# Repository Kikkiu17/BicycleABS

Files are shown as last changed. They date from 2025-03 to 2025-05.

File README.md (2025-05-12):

# Il progetto
Alla base del progetto c'è il microcontrollore **STM32F103C6T6**. Ho usato poi un servo **MGR996R** collegato alle pastiglie del freno, l'encoder magnetico **AS5600** per la misura della velocità, un sensore hall **3144EUA** per la misura dell'angolo del freno e uno schermo OLED con controllore SH1106. Il firmware è stato tutto scritto da me, compreso il [driver per lo schermo OLED](https://github.com/Kikkiu17/STM32_SH1106), tranne il driver per l'encoder AS5600. Tutti i pezzi sono stati stampati in 3D in PETG, PLA e TPU con una stampante Bambu Lab A1 Mini.

<p float="left">
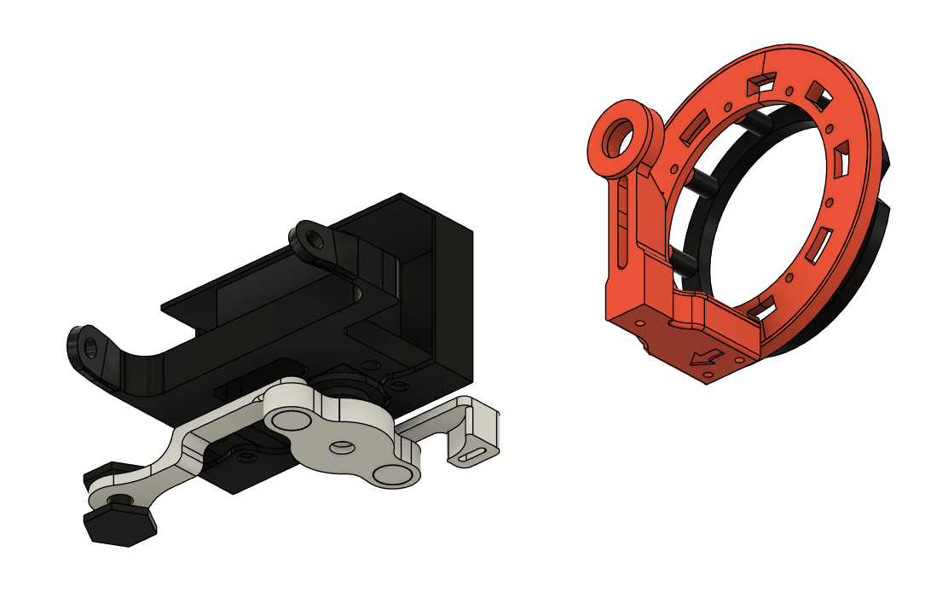
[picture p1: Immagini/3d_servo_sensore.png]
  
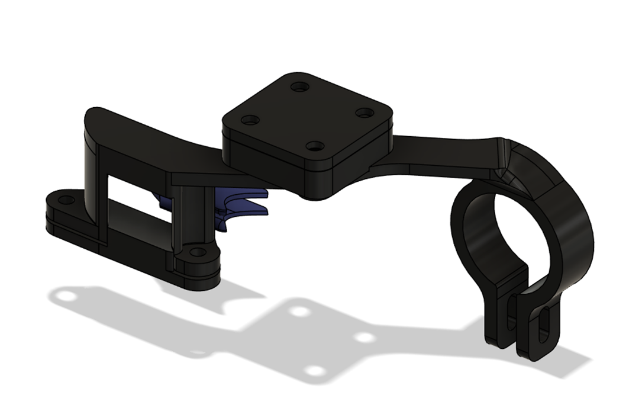
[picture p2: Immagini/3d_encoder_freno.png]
  
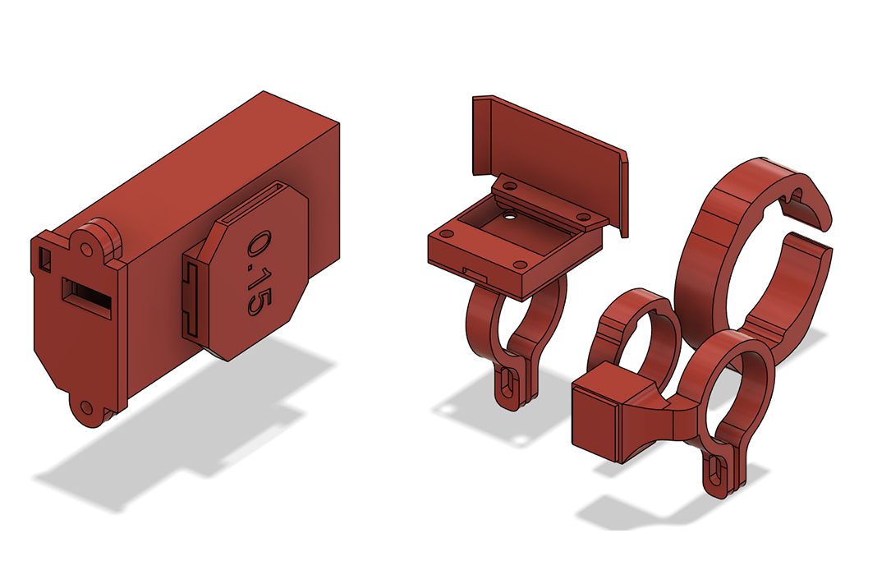
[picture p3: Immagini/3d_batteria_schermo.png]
  
</p>

In base all'angolo della maniglia del freno, il servo applica più o meno pressione alle pastiglie del freno, rallentando quindi la ruota e la bici. Quando la ruota si blocca, ad esempio se si frena tanto sullo sterrato, il microcontrollore rileva questa condizione e rilascia le pastiglie, in modo da sbloccare la ruota. Poi, riapplica pressione in modo da ricominciare a frenare e nel caso il ciclo continua.

Lo schermo OLED posto sul lato destro manubrio permette di vedere la velocità attuale della bici, i chilometri percorsi, il livello della batteria, lo stato delle luci (spente/accese/lampeggianti - la luce frontale, a cui ho tolto la batteria, era compresa con la bici, mentre la luce posteriore è fatta con due LED rossi) e se l'ABS si è attivato. Sul lato sinistro del manubrio invece è posto un pulsante che può essere usato per diverse cose. Se si fa una pressione breve si cambia la modalità delle luci (spente/accese/lampeggianti) in maniera ciclica. Se si fa una pressione lunga si entra nel menù, dal quale si possono modificare varie impostazioni (come l'angolo del servo, che quindi corrisponde alla pressione massima del freno, oppure la luminosità dello schermo), visualizzare diversi parametri di debug (come variabili interne dei TIMER del microcontrollore) e non (come la tensione della batteria).



# Costruzione - Hardware
Lo sviluppo dell'hardware è stato molto impegnativo. Il mio piano era modulare: sarei partito con la cosa più semplice, ovvero il supporto del servo, per fare un sistema **_brake by wire_**. In caso di successo, avrei continuato con il sensore dell'angolo della maniglia del freno (che d'ora in poi chiameremo **sensore freno**). In caso di successo, avrei continuato infine con il sensore di velocità della ruota. In questo modo avrei sprecato meno tempo possibile in caso di fallimento di qualche pezzo.

## Supporto e bracci servo
Per avvitare il supporto alla bici, ho sfruttato due buchi sul telaio apparentemente inutil in una posizione convenientemente vicina alle pastiglie del freno posteriore. Ho creato un supporto molto resistente e molto difficile da piegare in **PETG**, plastica adatta all'uso esterno (resistente ai raggi UV e al calore). Dopo ho realizzato dei bracci corti (in modo da massimizzare la coppia), da avvitare ai bracci del freno esistenti, **_print in place_**, ovvero che non necessitano di assemblaggio dopo la stampa (questo perché sono presenti due cerniere, difficili da fare resistenti e adatte all'assemblaggio). In questo modo il servo rimane ben saldo al telaio della bici e può fare tutta la forza che vuole.

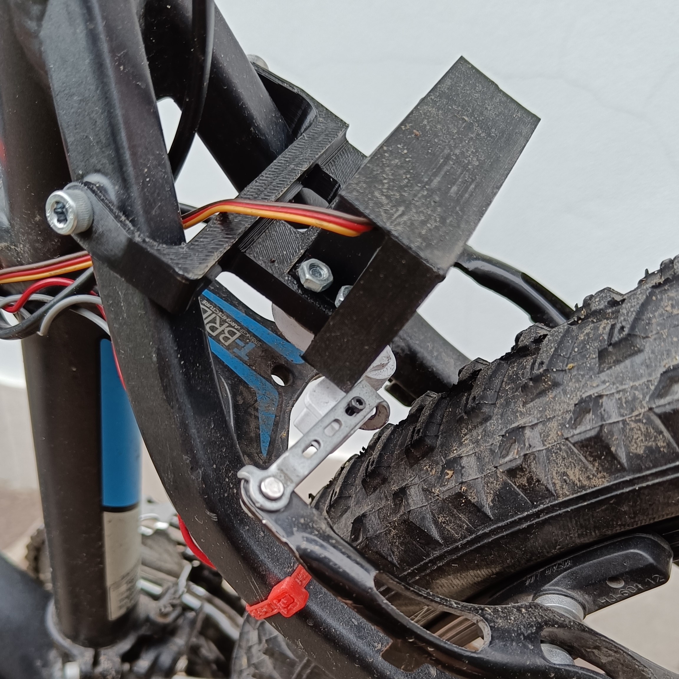
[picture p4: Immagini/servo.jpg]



## Sensore freno
Il sensore consiste in un magnete che ruota e una scheda con un chip che registra l'angolo del campo magnetico prodotto dal sensore. Non c'è però nessun punto comodo in cui montare né la parte fissa (il chip), né quella mobile (il magnete). Per il magnete quindi ho creato una sorta di morsa con dei gommini morbidi (quelli blu nella GIF) avvitata attorno alla maniglia del freno. Questa morsa ha un prolungamento su cui è situato il magnete, che si trova proprio sull'asse di rotazione della maniglia. Per il chip ho creato un supporto da avvitare al manubrio e che si estende fino a sopra il magnete, in modo da poter registrare il suo angolo. In base a quest'angolo, poi, determino l'angolo della maniglia e quindi quanto sto frenando. Dopo alcuni calcoli e controlli quest'angolo viene trasformato nell'angolo servo che viene direttamente inviato a quest'ultimo.



## Sensore di velocità
Il sensore di velocità comprende un semplice sensore **_hall_** (che rileva la presenza di un magnete o meno) e 30 magneti montati su un disco, a sua volta montato sulla ruota posteriore. Misurando quanti magneti vengono rilevati al secondo, si può determinare la velocità della ruota. Anche qui il problema è che non c'è nessun punto di montaggio comodo. Ho dovuto quindi creare il disco arancione in due pezzi in modo da poterlo mettere sull'asse di rotazione senza dover smontare l'intera ruota (il che significherebbe smontare anche il cambio... cosa che non avevo voglia di fare decine di volte) e per tenerlo fisso ad essa ho creato il pezzo nero che va ad avvitarsi dietro. In questo modo il pezzo arancione e il pezzo nero, avvitandosi, vanno a stringersi sui raggi del cerchio della ruota, effettivamente bloccandoli ad essa.

Il supporto del sensore **_hall_** è messo sull'asse della ruota e tenuto fermo con il dado originale che tiene fissa la ruota al telaio.

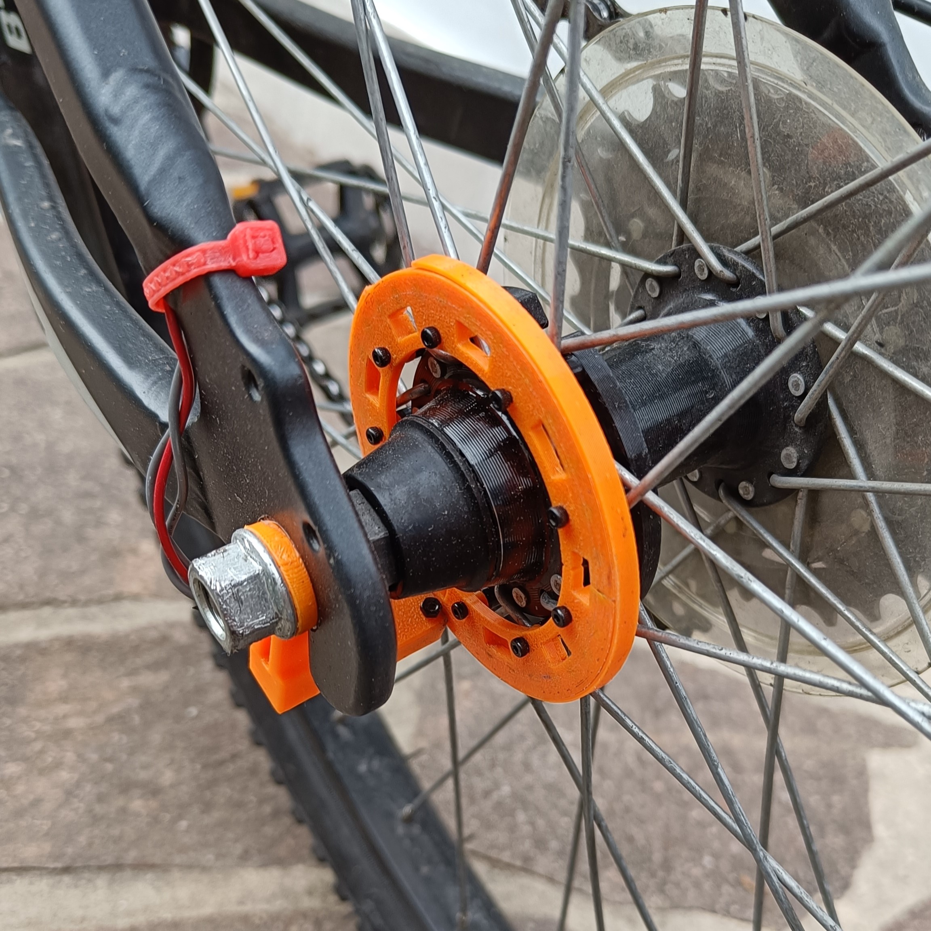
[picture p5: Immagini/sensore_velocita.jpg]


## Batteria
Ho anche creato un contenitore per una batteria LiPo 2S (7.4 V) che contiene anche un modulo per la ricarica della stessa. Ho voluto creare questo contenitore in modo da poter estrarre la batteria dalla bici in modo facile e veloce, così che posso portarla comodamente con me quando devo ricaricarla.



# Circuito elettronico
## Primo prototipo
Ho costruito il primo prototipo di circuito su una scheda millefori contemporaneamente allo sviluppo dei pezzi stampati in 3D. Dopo aver installato tutte le componenti e aver scritto parte del codice, ho realizzato che una scheda del genere non era adatta. Questo perché facendo pressione con il coperchio della scatola della scheda, oppure con qualche vibrazione (ad esempio passando dalla strada al marciapiede), il programma si bloccava e il servo rimaneva nella posizione di massima pressione. Dopo aver cercato per diverso tempo la causa del problema e non avendola trovata, ho deciso di abbandonare lo sviluppo su questa scheda. Questa però non è stata inutile perché mi ha permesso di testare le componenti e il programma, quindi sono passato allo sviluppo di una PCB (era solo un **_proof of concept_**).

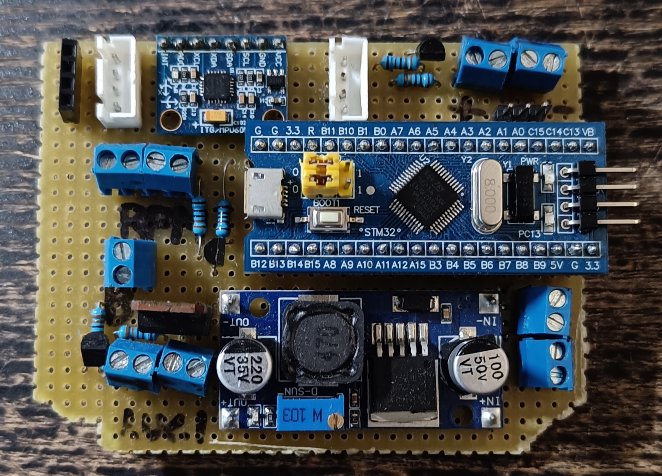
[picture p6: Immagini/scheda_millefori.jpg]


## PCB
Ho creato quindi la PCB con tutti i vari MOSFET per poter controllare la luce frontale e posteriore (luce posteriore che si accende quando si frena, mentre rimane spenta quando non si frena), il servo e il sensore di velocità. Ho messo poi due connettori per collegare lo schermo OLED e il sensore freno via I²C al microcontrollore. Ho lasciato anche dello spazio per il convertitore DC-DC dalla tensione della batteria a 6 V, ovvero la tensione per il servo, aggiungendo poi un altro regolatore di tensione per trasformare questi 6 V in 3.3 V per il microcontrollore.

Ho fatto qualche errore, ovvero che le impronte dei MOSFET non erano corrette, quindi quando ho assemblato la PCB ho dovuto ruotare questi componenti di 90°... però funziona.

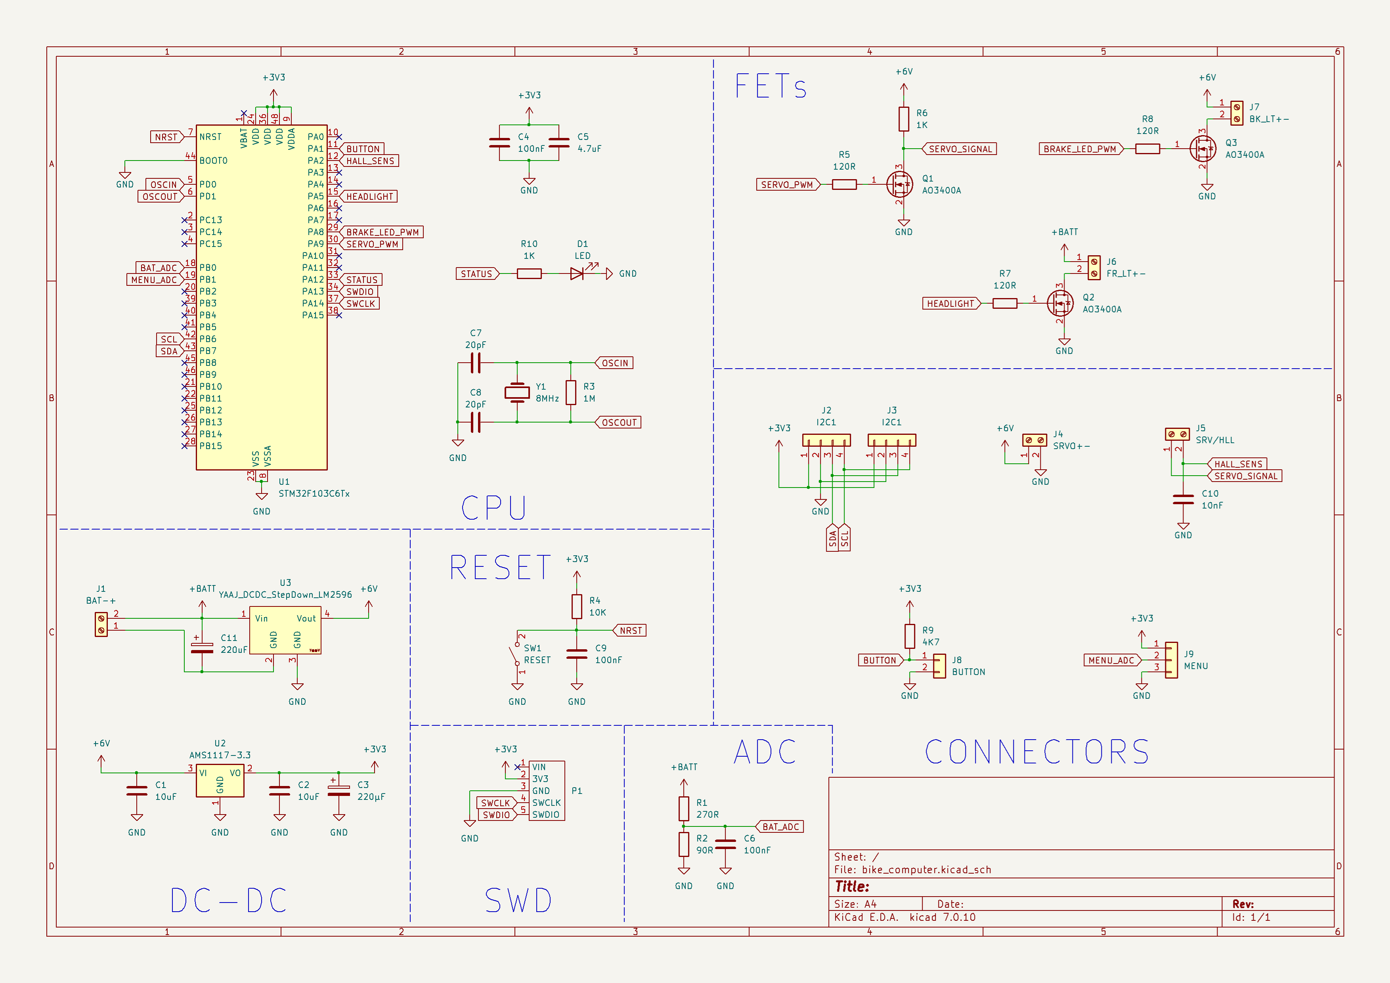
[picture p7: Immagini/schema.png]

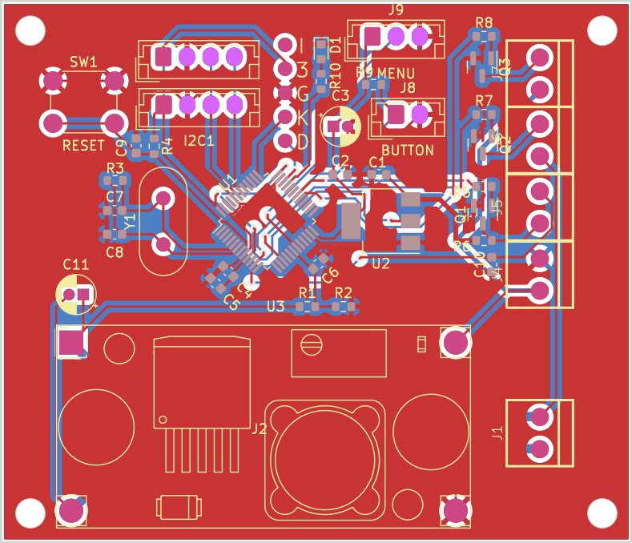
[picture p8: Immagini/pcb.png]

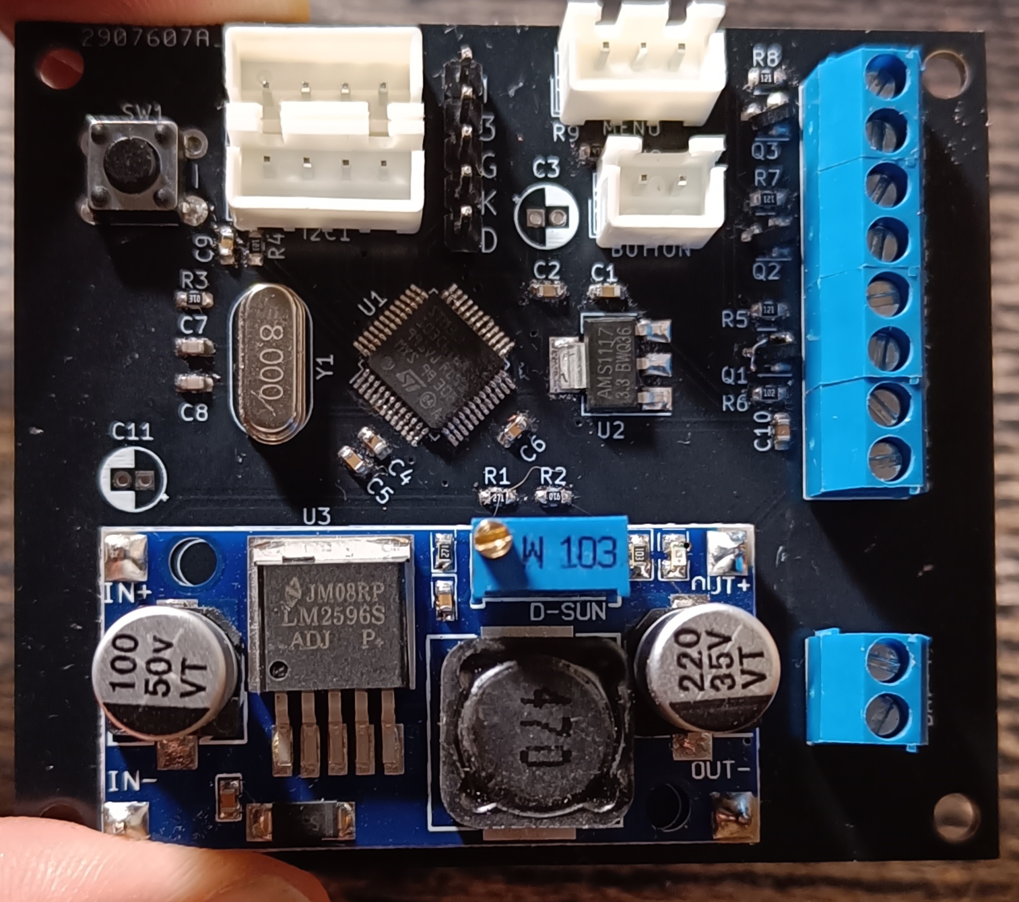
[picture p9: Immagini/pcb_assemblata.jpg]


# Firmware
## Calcolo velocità
L'output del sensore hall sulla ruota è un'onda quadra con un certo periodo. Questo periodo idealmente dovrebbe essere in microsecondi, così la conversione in secondi sarebbe molto semplice. C'è una limitazione: i timer dell'STM32F103 sono a 16-bit, quindi il valore massimo è 65535 - se questi fossero microsecondi, il periodo massimo registrabile sarebbe di circa 65 millisecondi. Facendo $f_{mag}=\frac{1}{T_{hall}}=\frac{1}{0.065}=15.38\text{ Hz}$ otteniamo la frequenza di rilevamento dei magneti dal sensore. Dato che abbiamo 30 magneti: $f_{ruota}=\frac{f_{mag}}{30}=\frac{15.38}{30}=0.51\text{ Hz}$.

Questo è un moto circolare, quindi per calcolare la velocità tangenziale bisogna fare: $v_{ruota}=\frac{r\Delta\theta}{\Delta t}=r\Delta\theta f_{ruota}$. Visto che abbiamo il periodo di un'intera rotazione, consideriamo che l'arco sia la circonferenza della ruota: $\Delta\theta=\frac{arco}{raggio}=\frac{2\pi r}{r}=2\pi$, quindi la formula iniziale diventa: $v_{ruota}=2\pi rf_{ruota}$.

Ora possiamo finalmente vedere la velocità minima registrabile, col periodo massimo di 65 millisecondi, ovvero 0.51 Hz. Considerando il raggio della ruota $r=0.34\text{ m}$: $v_{ruota}=2\pi (0.34\text{ m})(0.51\text{ Hz})=1.08\text{ m/s}$ ovvero 3.9 km/h. Questa è una velocità minima un po' troppo alta e quindi sarebbe difficile rilevare quando la ruota è effettivamente ferma.

Dobbiamo quindi aumentare il periodo massimo registrabile. Fino ad ora, abbiamo considerato che un "tick" equivalga a un microsecondo, ma ora dobbiamo farlo valere di più: ad esempio, se 1 tick = 2 microsecondi, allora il periodo massimo registrabile sarebbe il doppio, ovvero 130 millisecondi e utilizzando la formula di prima la velocità minima sarebbe di 1.97 km/h che è già più accettabile. Per fare questo calcolo nel software, dobbiamo considerare la frequenza del clock del timer, che è uguale per tutte le periferiche `APB1` e in questo caso è di `64 MHz`. Il valore di ogni tick è dato dalla frequenza di clock del timer diviso il "prescaler" `PSC`. Quindi, se il prescaler fosse di 128, avremmo $f_{TIM}=\frac{64000000}{128}=500\text{ kHz}$ quindi il tick sarebbe di 2 microsecondi. Ora dividiamo la frequenza di ogni tick per il numero di tick registrati ($k_{hall}$) e otteniamo la frequenza dei magneti.

Quindi:

$f_{TIM}=\frac{f_{APB1}}{PSC}$

$f_{mag}=\frac{f_{TIM}}{k_{hall}}$

$f_{ruota}=\frac{f_{mag}}{30}=\frac{\frac{f_{TIM}}{k_{hall}}}{30}=\frac{\frac{\frac{f_{APB1}}{PSC}}{k_{hall}}}{30}$ -> questa è infine, facendo qualche semplificazione, la formula usata nel programma, in C: `freq = ((float)(apb1_timer_clock / 10 / ((TIM2->PSC + 1) / 1000)) / (float)period) / 30.0` da cui si ricava la velocità.
## Rilevamento blocco
Ci sono due timer in azione: il primo è quello che è stato usato finora per calcolare la velocità della ruota. Il secondo viene usato per il rilevamento del blocco di essa. Il secondo timer ha una frequenza di 20 Hz, quindi viene controllato se la ruota è bloccata ogni 50 ms. Ogni 50 ms, quindi, il secondo timer controlla il periodo del primo timer: se questo è troppo alto, ovvero più alto del periodo del secondo timer, significa che la ruota ha rallentato molto, quindi si può considerare che stia scivolando. Inoltre, il primo timer, ogni volta che il sensore hall rileva un magnete, resetta il valore del secondo timer, quindi il rilevamento del blocco è migliore. L'ABS, quindi, se la ruota scivola, si attiva.

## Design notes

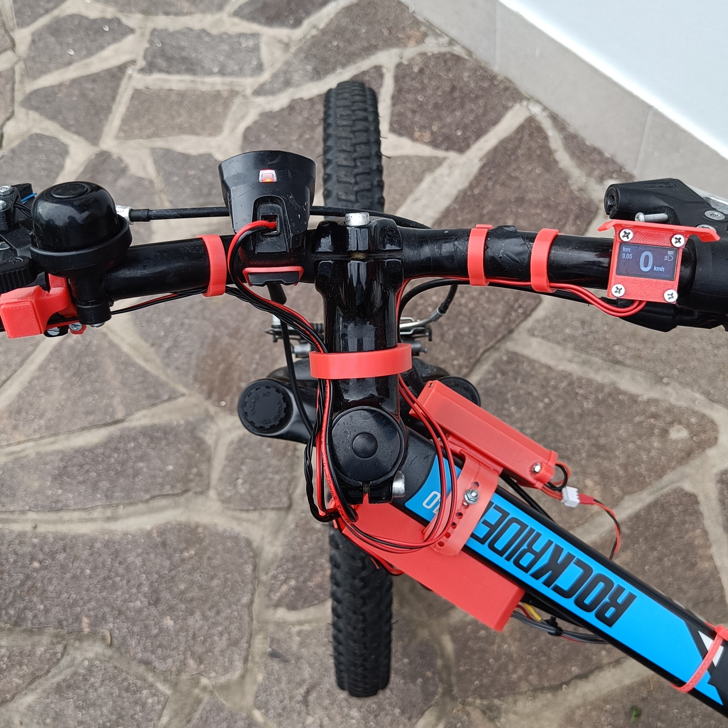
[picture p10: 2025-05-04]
Immagini/manubrio.jpg

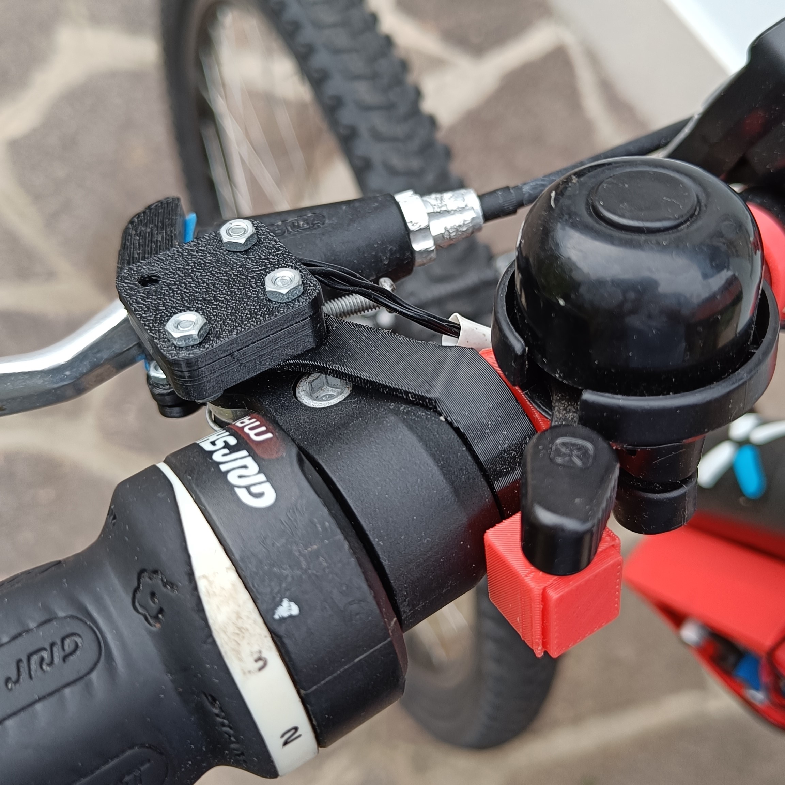
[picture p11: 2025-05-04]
Immagini/encoder_freno.jpg

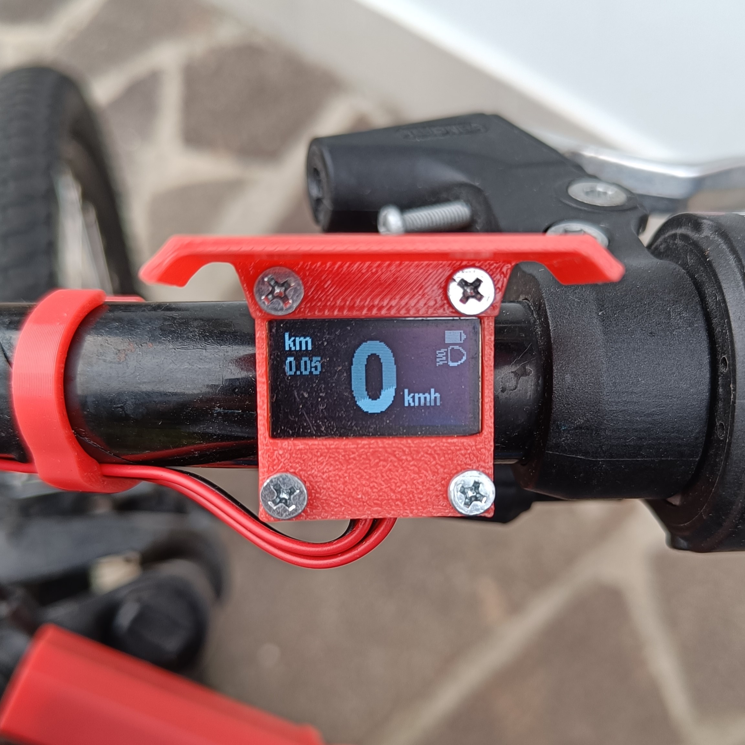
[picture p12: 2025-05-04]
Immagini/schermo.jpg

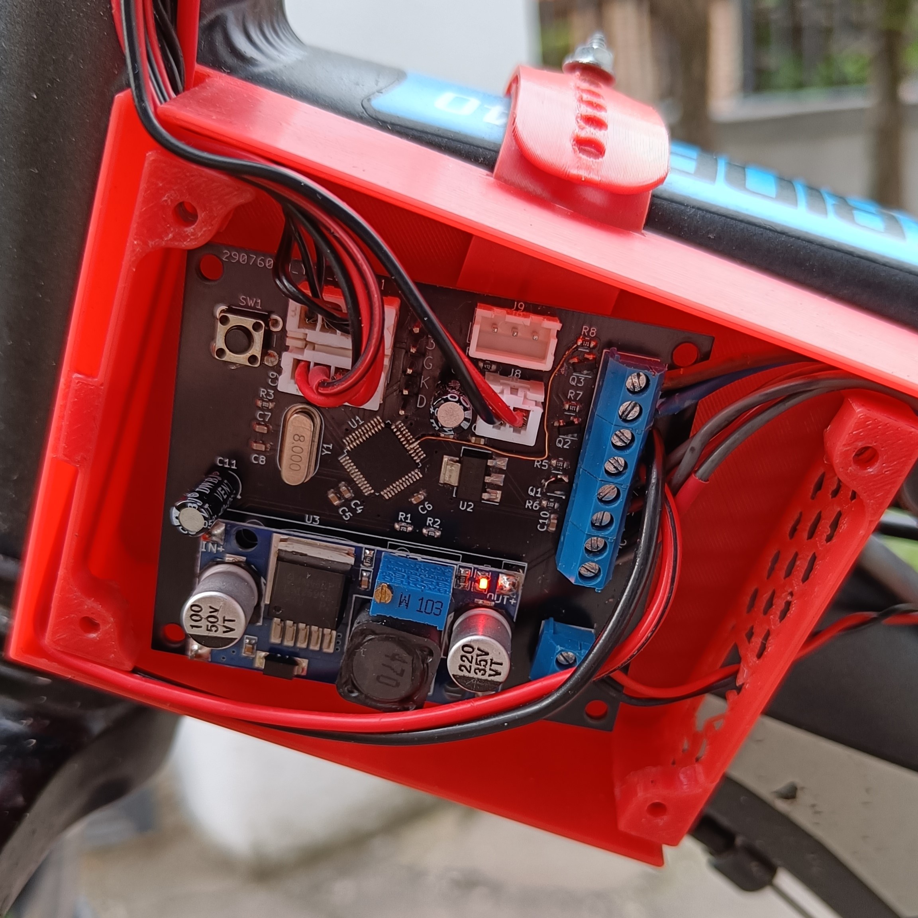
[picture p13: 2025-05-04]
Immagini/pcb_montata.jpg

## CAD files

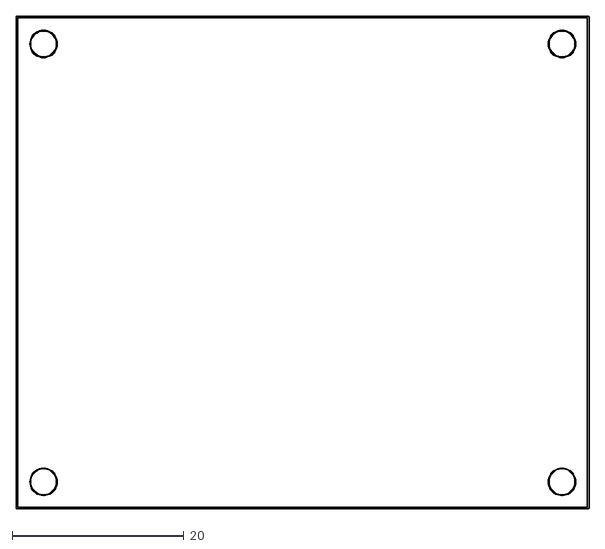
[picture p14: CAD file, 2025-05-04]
Hardware/PCB/bike_computer_gerber/bike_computer-Edge_Cuts.dxf
66.8 x 57.5

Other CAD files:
Hardware/PCB/bike_computer_gerber/bike_computer-F_Paste.dxf

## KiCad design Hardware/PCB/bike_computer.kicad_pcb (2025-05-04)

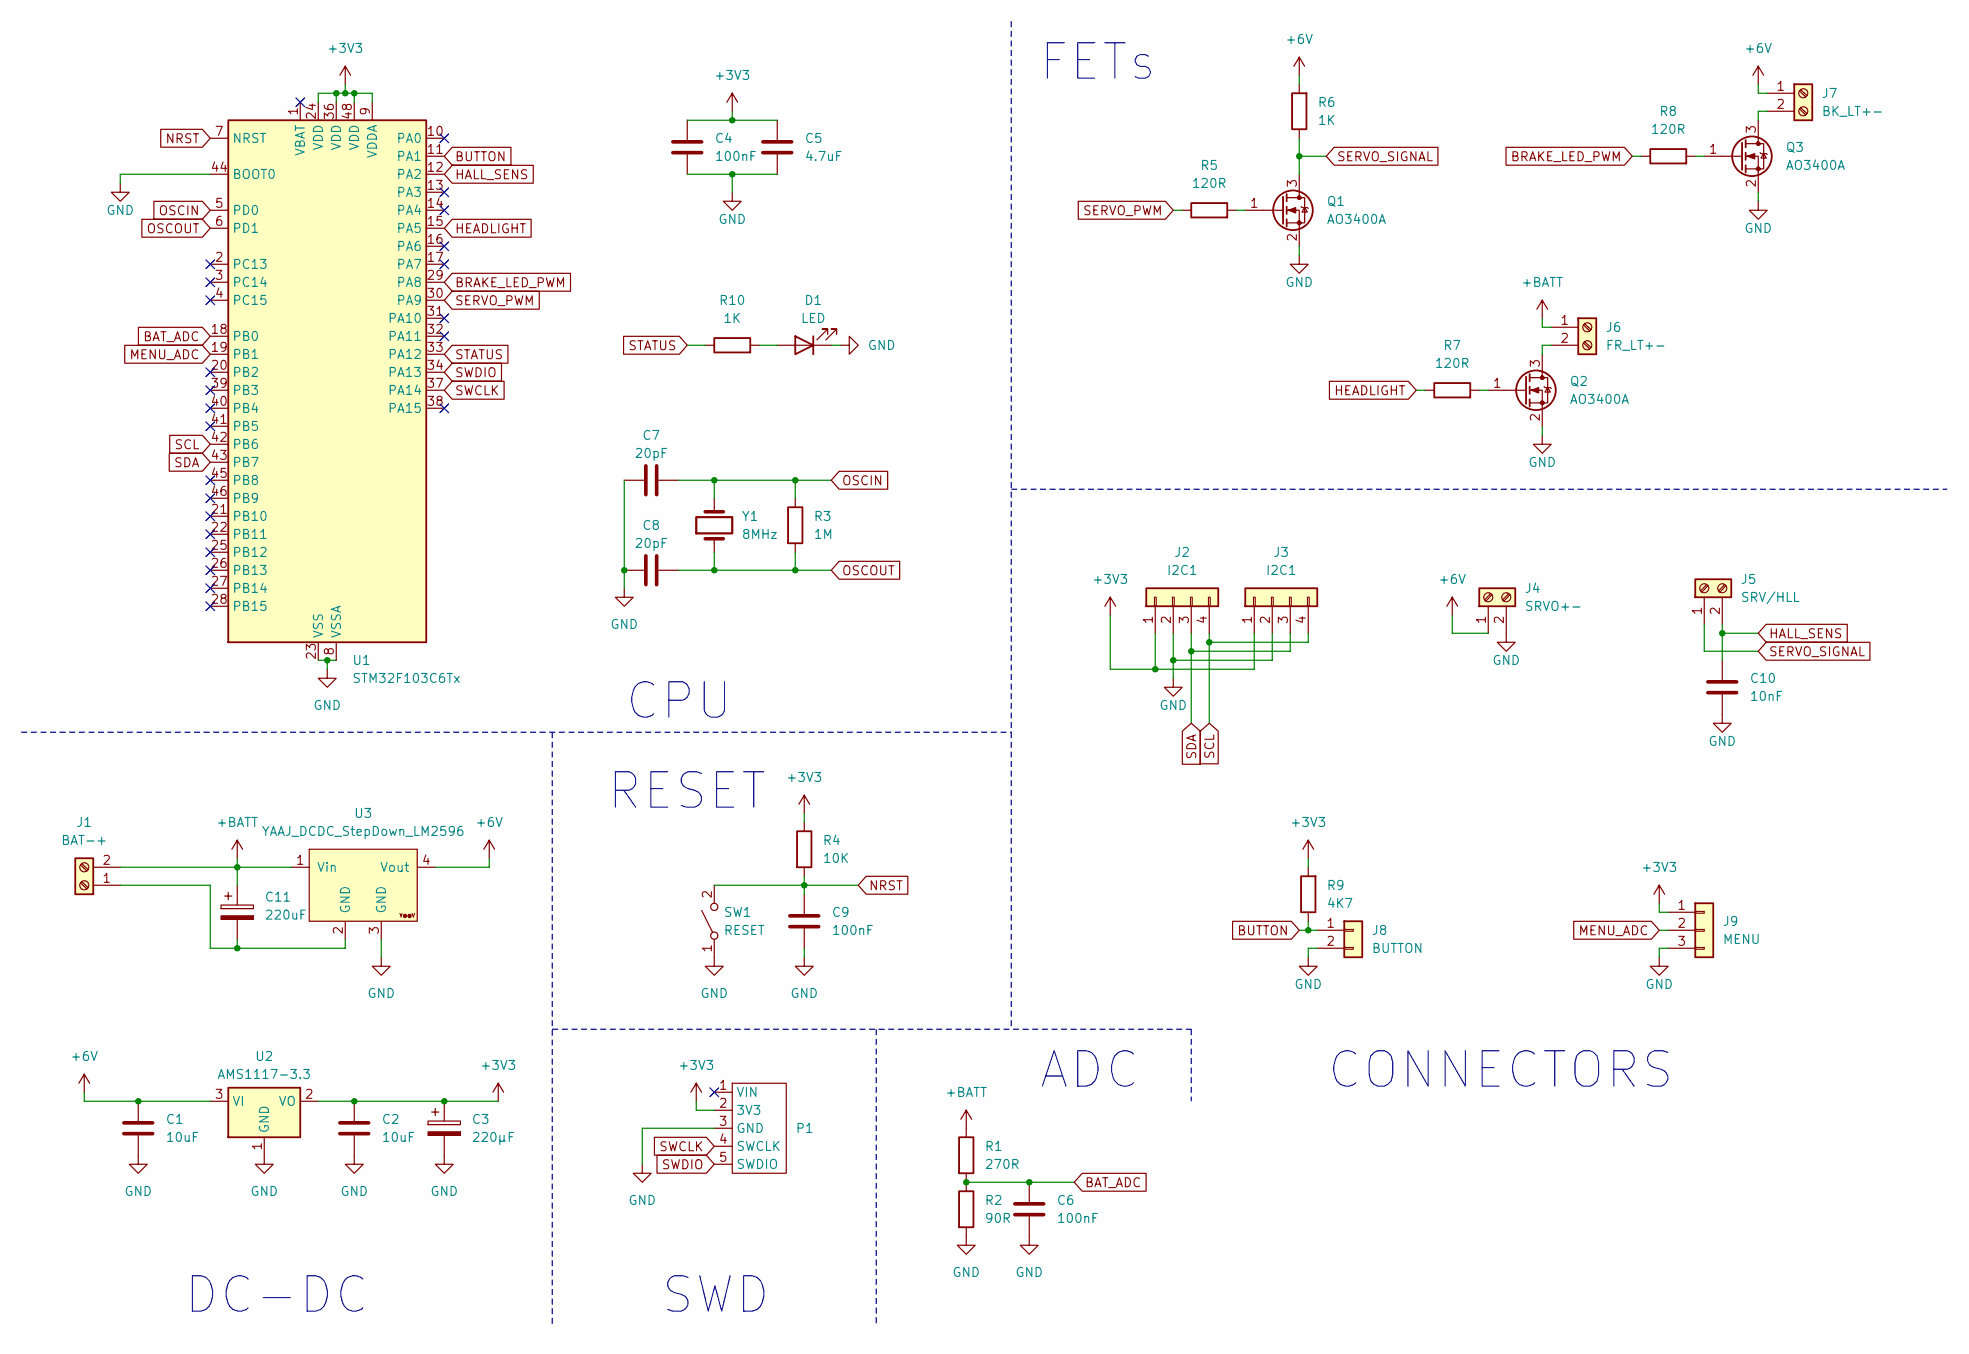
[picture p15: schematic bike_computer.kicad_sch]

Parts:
C1, C2: 10uF; C_0603_1608Metric
C3: 220µF; CP_Radial_D4.0mm_P1.50mm
C4, C6, C9: 100nF; C_0603_1608Metric
C5: 4.7uF; C_0603_1608Metric
C7, C8: 20pF; C_0603_1608Metric
C10: 10nF; C_0603_1608Metric
C11: 220uF; CP_Radial_D4.0mm_P1.50mm
D1: LED; LED_0603_1608Metric
J1: BAT-+; screw_2p_small
J2, J3: I2C1; JST_EH_B4B-EH-A_1x04_P2.50mm_Vertical
J4: SRVO+-; screw_2p_small
J5: SRV/HLL; screw_2p_small
J6: FR_LT+-; screw_2p_small
J7: BK_LT+-; screw_2p_small
J8: BUTTON; JST_EH_B2B-EH-A_1x02_P2.50mm_Vertical
J9: MENU; JST_EH_B3B-EH-A_1x03_P2.50mm_Vertical
P1: stm_headers
Q1, Q2, Q3: AO3400A; SOT-23
R1: 270R; R_0603_1608Metric
R2: 90R; R_0603_1608Metric
R3: 1M; R_0603_1608Metric
R4: 10K; R_0603_1608Metric
R5, R7, R8: 120R; R_0603_1608Metric
R6, R10: 1K; R_0603_1608Metric
R9: 4K7; R_0603_1608Metric
SW1: RESET; SW_PUSH_6mm
U1: STM32F103C6Tx; LQFP-48_7x7mm_P0.5mm
U2: AMS1117-3.3; SOT-223-3_TabPin2
U3: YAAJ_DCDC_StepDown_LM2596
Y1: 8MHz; Crystal_HC49-4H_Vertical

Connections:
+3V3: C2.1, C3.1, C4.1, C5.1, J2.1, J3.1, J9.1, P1.2 (3V3), R4.1, R9.2, U1.9 (VDDA), U1.24 (VDD), U1.36 (VDD), U1.48 (VDD), U2.2 (VO)
+6V: C1.1, J4.1, J7.1, R6.2, U2.3 (VI), U3.4 (Vout)
+BATT: C11.1, J1.2, J6.1, R1.1, U3.1 (Vin)
BAT_ADC: C6.1, R1.2, R2.1, U1.18 (PB0)
BRAKE_LED_PWM: R8.1, U1.29 (PA8)
BUTTON: J8.1, R9.1, U1.11 (PA1)
GND: C1.2, C2.2, C3.2, C4.2, C5.2, C6.2, C7.1, C8.1, C9.2, C10.2, D1.1 (K), J2.2, J3.2, J4.2, J8.2, J9.3, P1.3 (GND), Q1.2 (S), Q2.2 (S), Q3.2 (S), R2.2, SW1.1 (A), U1.8 (VSSA), U1.23 (VSS), U1.35 (VSS), U1.44 (BOOT0), U1.47 (VSS), U2.1 (GND), U3.3 (GND)
HALL_SENS: C10.1, J5.2, U1.12 (PA2)
HEADLIGHT: R7.1, U1.15 (PA5)
MENU_ADC: J9.2, U1.19 (PB1)
NRST: C9.1, R4.2, SW1.2 (B), U1.7 (NRST)
unnamed: C11.2, J1.1, U3.2 (GND)
unnamed: D1.2 (A), R10.2
unnamed: Q1.1 (G), R5.2
unnamed: J6.2, Q2.3 (D)
unnamed: Q2.1 (G), R7.2
unnamed: J7.2, Q3.3 (D)
unnamed: Q3.1 (G), R8.2
OSCIN: C7.2, R3.1, U1.5 (PD0), Y1.2
OSCOUT: C8.2, R3.2, U1.6 (PD1), Y1.1
SCL: J2.4, J3.4, U1.42 (PB6)
SDA: J2.3, J3.3, U1.43 (PB7)
SERVO_PWM: R5.1, U1.30 (PA9)
SERVO_SIGNAL: J5.1, Q1.3 (D), R6.1
STATUS: R10.1, U1.33 (PA12)
SWCLK: P1.4 (SWCLK), U1.37 (PA14)
SWDIO: P1.5 (SWDIO), U1.34 (PA13)

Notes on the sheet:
FETs
CPU
RESET
ADC
DC-DC
SWD
CONNECTORS

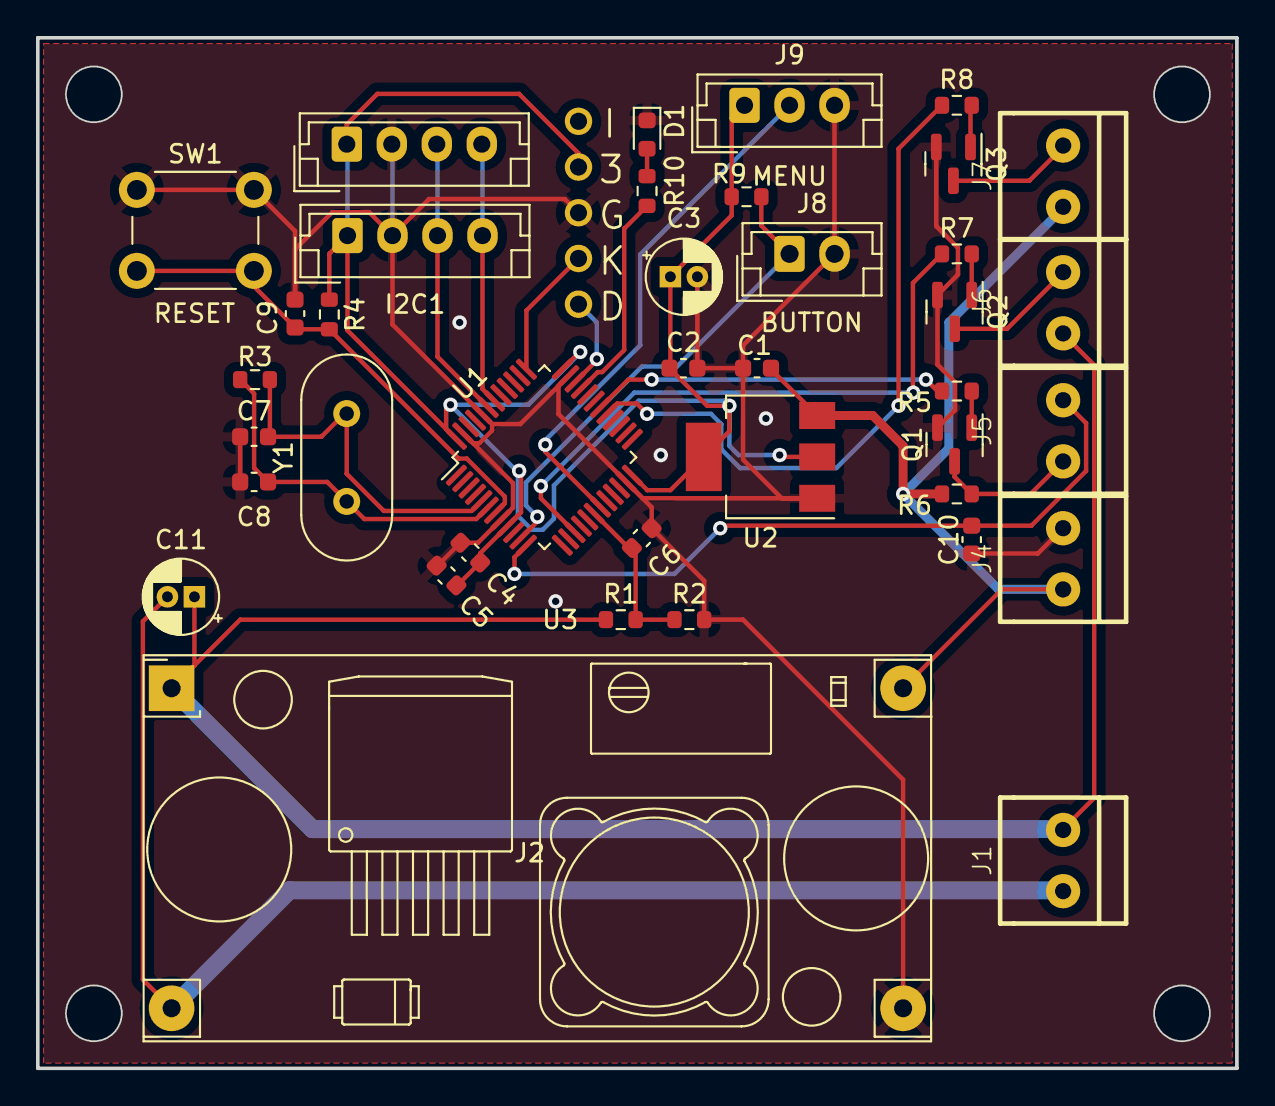
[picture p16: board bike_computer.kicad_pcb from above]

Board: 2 copper layers, 66.6 x 57.3 mm, 40 parts (0 on the bottom side), 27 nets.

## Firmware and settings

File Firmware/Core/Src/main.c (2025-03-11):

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
/* Includes ------------------------------------------------------------------*/
#include "main.h"
#include "adc.h"
#include "i2c.h"
#include "tim.h"
#include "gpio.h"

/* USER CODE BEGIN Includes */
#include <inttypes.h>
#include <stdio.h>
#include <stdlib.h>
#include "As5600.h"
#include "servo.h"
#include "stm32f1xx_ll_exti.h"

#include "../sh1106/sh1106.h"
#include "../bitmaps/bitmaps.h"
#include "../menu/menu.h"
#include "../settings.h"
#include "../button/button.h"
/* USER CODE END Includes */


/* USER CODE BEGIN PV */
uint32_t kmh = 0;
int32_t last_kmh = 0;
int32_t kmh_diff = 0;
uint32_t brake_lever_angle = 0;
int32_t servo_angle = 0;
int32_t min_servo_angle = 0;

bool abs_on = false;				// if true, the ABS is currently operating
uint32_t abs_time = 0;			// time of the ABS activation

uint64_t apb1_timer_clock = 0;
uint64_t timer_update_constant = 0;
uint64_t period = 0;
uint32_t last_period = 0;
uint32_t last_capture_time = 0;

uint32_t light_mode = 0;

uint32_t last_capture_value = 0;
float last_freq = 0.00;
float current_freq = 0.00;
float avg_freq = 0.00;

char text[50];
/* USER CODE END PV */

void SystemClock_Config(void);
/* USER CODE BEGIN 0 */
long mapInt(uint32_t x, int32_t in_min, int32_t in_max, int32_t out_min, int32_t out_max) {
  return (x - in_min) * (out_max - out_min) / (in_max - in_min) + out_min;
}


uint32_t constrain(uint32_t value, uint32_t max, uint32_t min)
{
	if (value >= max)
		return max;
	else if (value <= min)
		return min;
	return value;
}


uint32_t offset(uint32_t value, uint32_t offset)
{
	if (value <= offset)
		return 0;
	else
		return value - offset;
}

/* USER CODE END 0 */

/**
  * @brief  The application entry point.
  * @retval int
  */
int main(void)
{

  /* MCU Configuration--------------------------------------------------------*/

  /* Reset of all peripherals, Initializes the Flash interface and the Systick. */
  HAL_Init();

  /* Configure the system clock */
  SystemClock_Config();

  /* Initialize all configured peripherals */
  MX_GPIO_Init();
  MX_TIM1_Init();
  MX_TIM2_Init();
  MX_TIM3_Init();
  MX_I2C1_Init();
  MX_ADC1_Init();
  /* USER CODE BEGIN 2 */
  HAL_TIM_PWM_Start(&htim1, TIM_CHANNEL_1);
  HAL_TIM_PWM_Start(&htim1, TIM_CHANNEL_2);
  HAL_TIM_IC_Start_IT(&htim2, TIM_CHANNEL_3);
  //HAL_TIM_PWM_Start(&htim3, TIM_CHANNEL_1);
  HAL_TIM_Base_Start_IT(&htim3);
  HAL_ADCEx_Calibration_Start(&hadc1);

  apb1_timer_clock = HAL_RCC_GetPCLK1Freq() * 2 / 100;
  timer_update_constant = (TIM3->PSC + 1) * (TIM3->ARR + 1) * (720 / ((TIM2->PSC + 1) / 1000));

  SERVO_Write(&htim1, TIM_CHANNEL_2, servo_max, 1);

  SH1106_Init();
  SH1106_SetBrightness(screen_brightness);
  SH1106_ClearScreen();

  AS5600_TypeDef as5600;
  AS5600_Init();
  Get_Magnet_Status(&as5600);
  bool magnet_status = as5600.Status_Magnet;

  if (magnet_status) SH1106_WriteChars(0, 0, "magnete ok", 10, Arial_12pt, 1);
  else
  {
	  SH1106_WriteChars(0, 0, "Magnete NON OK\nPremi un tasto\nper continuare", 44, Arial_12pt, 1);
	  while (1)
	  {
		  if (!HAL_GPIO_ReadPin(BTN_IN_GPIO_Port, BTN_IN_Pin))
			  break;
	  }
  }

  SH1106_ClearScreen();
  SH1106_SetScreenAutoUpdate(false);

  uint32_t flashing_lights_time = 0;
  uint32_t deltat = 0;
  uint32_t last_time = 0;
  float traveled_meters = 0.00;
  uint32_t mvbat = 0;
  bool show_low_bat = false;
  char decimal_travel_string[2];
  uint32_t raw_brake_lever_angle = 0;
  /* USER CODE END 2 */

  /* Infinite loop */
  /* USER CODE BEGIN WHILE */
  while (1)
  {
	  deltat = uwTick - last_time;
	  last_time = uwTick;

	  // clear screen
	  SH1106_FillScreen(BLACK);

	  Get_Raw_Angle(&as5600);
	  raw_brake_lever_angle = as5600.Raw_sensor_Angle;
	  brake_lever_angle = offset(raw_brake_lever_angle, BRAKE_ANGLE_OFFSET);

	  if (!abs_on)
	  {
		  servo_angle = mapInt((int16_t)(brake_lever_angle), 0, BRAKE_ANGLE_MAX, servo_max, servo_min);
		  servo_angle = constrain(servo_angle, servo_max, servo_min);
	  }
	  else
	  {
		  // increase brake pressure gradually
		  if (servo_angle - SERVO_ABS_BRAKE_RATE > min_servo_angle && min_servo_angle >= servo_min)
			  servo_angle -= SERVO_ABS_BRAKE_RATE;
		  else abs_on = false;
	  }

	  if (mvbat > LOW_BATTERY_THRESHOLD)
	  {
		  if (servo_enabled)
			  SERVO_Write(&htim1, TIM_CHANNEL_2, servo_angle, 1);
		  else
		  {
			  if (!servo_hold)
				  SERVO_Write(&htim1, TIM_CHANNEL_2, servo_max, 1);
		  }
	  }
	  else
		  SERVO_Write(&htim1, TIM_CHANNEL_2, servo_max, 1);

	  // disable abs if brake lever is released
	  if (brake_lever_angle <= BRAKE_THRESHOLD || (kmh == 0 && brake_lever_angle <= BRAKE_THRESHOLD))
		  abs_on = false;

	  // -------------------- TRAVEL --------------------
	  traveled_meters += (float)kmh / 3.6 * (float)deltat / 1000.0;
	  uint32_t int_travel = traveled_meters / 1000;
	  uint32_t decimal_travel = traveled_meters - int_travel * 1000;

	  // -------------------- BATTERY VOLTAGE --------------------
	  HAL_ADC_Start(&hadc1);
	  HAL_ADC_PollForConversion(&hadc1, HAL_MAX_DELAY);
	  uint32_t raw_value = HAL_ADC_GetValue(&hadc1);
	  float vbat = (float)raw_value / 4096.0 * 3.3 * 4;
	  mvbat = vbat * 1000;
	  uint32_t int_volt = vbat;
	  uint32_t decimal_volt = vbat * 100 - int_volt * 100;

	  // -------------------- HEADLIGHT AND BRAKE LIGHT --------------------
	  switch (light_mode)
	  {
	  case 0:
	  {
		  // -------------------- LIGHTS OFF --------------------
		  HAL_GPIO_WritePin(FRONT_LIGHTS_GPIO_Port, FRONT_LIGHTS_Pin, GPIO_PIN_RESET);

		  if (servo_angle <= BRAKE_THRESHOLD)
			  __HAL_TIM_SET_COMPARE(&htim1, TIM_CHANNEL_1, TIM1->ARR);
		  else
			  __HAL_TIM_SET_COMPARE(&htim1, TIM_CHANNEL_1, 0);

		  break;
	  }
	  case 1:
	  {
		  // -------------------- LIGHTS ON --------------------
		  HAL_GPIO_WritePin(FRONT_LIGHTS_GPIO_Port, FRONT_LIGHTS_Pin, GPIO_PIN_SET);

		  if (servo_angle <= BRAKE_THRESHOLD)
			  __HAL_TIM_SET_COMPARE(&htim1, TIM_CHANNEL_1, TIM1->ARR);
		  else
			  __HAL_TIM_SET_COMPARE(&htim1, TIM_CHANNEL_1, brake_light_pwm_period);

		  break;
	  }
	  case 2:
	  {
		  // -------------------- FLASHER --------------------
		  if (uwTick - flashing_lights_time > LIGHT_FLASHER_TIME)
		  {
			  flashing_lights_time = uwTick;

			  if (__HAL_TIM_GET_COMPARE(&htim1, TIM_CHANNEL_1) == TIM1->ARR)
				  __HAL_TIM_SET_COMPARE(&htim1, TIM_CHANNEL_1, 0);
			  else
				  __HAL_TIM_SET_COMPARE(&htim1, TIM_CHANNEL_1, TIM1->ARR);
		  }

		  break;
	  }
	  case 3:
	  {
		  light_mode = 0;
		  break;
	  }
	  }

	  // -------------------- DRAWING FUNCTIONS --------------------

	  if (mvbat > LOW_BATTERY_THRESHOLD)
	  {
		  // -------------------- BUTTON --------------------
		  uint8_t press_type = BUTTON_Handle(BTN_IN_GPIO_Port, BTN_IN_Pin, 1);

		  if (MENU_Update() != 0)
		  {
			  // -------------------- MENU --------------------
			  MENU_UpdateData(raw_brake_lever_angle, brake_lever_angle, servo_angle, mvbat);
			  MENU_UpdateDebug(kmh, period, last_capture_value, last_capture_time, current_freq, avg_freq);

			  if (press_type == SHORT_PRESS)
				  MENU_ButtonShortPress();
			  else if (press_type == LONG_PRESS)
				  MENU_ButtonLongPress();
			  SH1106_UpdateEntireFrame();
		  }
		  else
		  {
			  // -------------------- MAIN SCREEN --------------------
			  if (press_type == LONG_PRESS)
				  MENU_Set(1);
			  else if (press_type == SHORT_PRESS)
				  light_mode++;


			  // -------------------- LIGHT INDICATOR --------------------
			  if (light_mode == 1)
				  SH1106_DrawBitmap(light_img, 106, 12, 20, 15, false);
			  else if (light_mode == 2)
			  {
				  if (__HAL_TIM_GET_COMPARE(&htim1, TIM_CHANNEL_1) == TIM1->ARR)
					  SH1106_DrawBitmap(light_img, 106, 12, 20, 15, false);
			  }


			  // -------------------- SPEED --------------------
			  memset(text, 0, sizeof(text));
			  sprintf(text, "%" PRIu32, kmh);
			  uint32_t speed_width = SH1106_GetTextWidth(text, 2, Arial_48pt);
			  if (uwTick - abs_time < 2250)
			  {
				  sprintf(text, "%" PRIu32, kmh);
				  speed_width = SH1106_GetTextWidth(text, 3, Arial_48pt);
				  SH1106_WriteChars(64 - speed_width / 2, 7, text, 3, Arial_48pt, false);

				  SH1106_DrawBitmap(abs_img, 4, 34, 33, 25, false);
			  }
			  else
			  {
				  SH1106_WriteChars(64 - speed_width / 2, 7, text, 2, Arial_48pt, false);
			  }
			  sprintf(text, "kmh");
			  SH1106_WriteChars(68 + speed_width / 2, 38, text, 3, Arial_12pt, false);


			  // -------------------- TRAVEL --------------------
			  memset(text, 0, 6);
			  sprintf(text, "%" PRIu32, decimal_travel);
			  leftPadding(decimal_travel_string, text, 3, '0');
			  sprintf(text, "km:\n%" PRIu32 ".%s", int_travel, decimal_travel_string);
			  SH1106_WriteChars(4, 0, text, 8, Arial_12pt, false);


			  // -------------------- BATTERY --------------------
			  uint32_t battery_charge = mapInt(vbat * 1000, LOW_BATTERY_THRESHOLD, CHARGED_BATTERY_THRESHOLD, 0, BATTERY_CHARGE_WIDTH);
			  SH1106_DrawBitmap(battery_img, 112, 2, 15, 8, false);
			  SH1106_DrawRect(112, 2, battery_charge, 8, BLUE, false);
		  }

	  }
	  else
	  {
		  light_mode = 0;

		  if (uwTick - flashing_lights_time > LIGHT_FLASHER_TIME * 2)
		  {
			  flashing_lights_time = uwTick;

			  show_low_bat = !show_low_bat;
		  }

		  if (show_low_bat)
		  {
			  // LOW BATTERY
			  SH1106_DrawBitmap(battery_img, 108, 6, 15, 8, false);

			  memset(text, 0, sizeof(text));
			  sprintf(text, "BATTERIA\nSCARICA\n%" PRIu32 ".%" PRIu32 "V", int_volt, decimal_volt);
			  SH1106_WriteChars(6, 8, text, 22, Arial_12pt, false);
		  }
	  }

	  SH1106_UpdateEntireFrame();
    /* USER CODE END WHILE */

    /* USER CODE BEGIN 3 */
  }
  /* USER CODE END 3 */
}

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
/* USER CODE BEGIN 4 */
void HAL_TIM_PeriodElapsedCallback(TIM_HandleTypeDef* htim)
{
	if (htim->Instance == TIM3)
	{
		// lock-up check cut-off is around 6 kmh
		if (kmh <= 6)
		{
			if (last_capture_time > uwTick) return;
			// 125 is a calibration value found during testing
			// 125 ms (calibrated; around 150 measured period) is the period
			// around which there is the transition
			// between 2 and 1 kmh (see kmh formula in callback below)
			if (uwTick - last_capture_time > 125)
				kmh = 0;
		}
		// if ((period (+ 3, optionally)) * apb1_timer_clock < timer_update_constant)
		// this is a simplified form of:
		// period * 1000 / 1200 < ((TIM3->PSC + 1) * (TIM3->ARR + 1)) * 1000 / apb1_timer_clock.
		// 3 is a calibration value found in testing to create a deadzone for the
		// lock-up detector. TIM3 is cleared every time an interrupt occurs
		else if ((period) * apb1_timer_clock < timer_update_constant)
		{
			kmh = 0;
			if (brake_lever_angle <= BRAKE_THRESHOLD)
			{
				HAL_GPIO_TogglePin(GPIOC, GPIO_PIN_13);
				// lock-up
				if (abs_enabled)
					abs_on = true;		// true until the bike stops or no brake is applied
				abs_time = uwTick;

				min_servo_angle = servo_angle;
				servo_angle = servo_max;
				SERVO_Write(&htim1, TIM_CHANNEL_2, servo_angle, true);	// release the brake
			}
		}
	}
}


void HAL_TIM_IC_CaptureCallback(TIM_HandleTypeDef *htim)
{
	// capture compare is from TIM2
	if (htim->Channel == HAL_TIM_ACTIVE_CHANNEL_3 && htim->Instance == TIM2)
	{
		uint32_t capture_value = HAL_TIM_ReadCapturedValue(htim, TIM_CHANNEL_3);
		// avoids weird numbers when TIM2 overflows
		if (abs((int)capture_value - (int)last_capture_value) > capture_value / 2)
		{
			last_capture_value = capture_value;
			return;
		}

		__HAL_TIM_SET_COUNTER(&htim3, 0);	// ABS timer reset

		if (last_capture_value > (last_period + capture_value))
			return;

		period = (last_period + capture_value - last_capture_value) / 2;

		last_capture_value = capture_value;
		last_period = period;
		last_capture_time = uwTick;

		// 1 / ((period * 30) / 1200)
		// there are 30 magnets in the encoder and TIM2 clocks at 1200 Hz

		// use this for smoother speed indication but less accurate
		// stop detection

		// (1.0 / 30.0 * (float)(720 / ((TIM2->PSC + 1) / 1000) * 1000))
		// is like 1 / 30 * (clock frequency)
		// if PSC = 15000: 1 / 30 * 4800 = 160

		current_freq = (1.0 / 30.0 * (float)(720 / ((TIM2->PSC + 1) / 1000) * 100)) / (float)period;
		avg_freq = (current_freq + last_freq) / 2.0;
		if (current_freq == 0)
			avg_freq = 0;
		//float freq = 40.0 / (float)period;

		// 2πrƒ = [m/s] * 3.6 = [km/h]
		kmh = 2 * 3.14 * avg_freq * 0.34 * 3.6;
		if (kmh > MAX_SPEED)
			kmh = 0;
		//if (kmh <= 3) kmh = 0;
		last_freq = avg_freq;
	}
}
/* USER CODE END 4 */
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


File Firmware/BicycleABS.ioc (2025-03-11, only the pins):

Mcu.UserName=STM32F103C6Tx
PA1.GPIO_Label=BTN_IN
PA1.Signal=GPIO_Input
PA13.Signal=SYS_JTMS-SWDIO
PA14.Signal=SYS_JTCK-SWCLK
PA2.GPIO_Label=HALL_IN
PA2.Signal=S_TIM2_CH3
PA5.GPIO_Label=FRONT_LIGHTS
PA5.Signal=GPIO_Output
PA8.GPIO_Label=BRAKE_LIGHT
PA8.Signal=S_TIM1_CH1
PA9.GPIO_Label=SERVO_OUT
PA9.Signal=S_TIM1_CH2
PB0.GPIO_Label=BAT_ADC
PB0.Signal=ADCx_IN8
PB6.Signal=I2C1_SCL
PB7.Signal=I2C1_SDA
PC13-TAMPER-RTC.GPIO_Label=BOARD_LED
PC13-TAMPER-RTC.Signal=GPIO_Output
PD0-OSC_IN.Signal=RCC_OSC_IN
PD1-OSC_OUT.Signal=RCC_OSC_OUT

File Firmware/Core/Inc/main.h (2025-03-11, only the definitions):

#define BOARD_LED_Pin GPIO_PIN_13
#define BOARD_LED_GPIO_Port GPIOC
#define BTN_IN_Pin GPIO_PIN_1
#define BTN_IN_GPIO_Port GPIOA
#define HALL_IN_Pin GPIO_PIN_2
#define HALL_IN_GPIO_Port GPIOA
#define FRONT_LIGHTS_Pin GPIO_PIN_5
#define FRONT_LIGHTS_GPIO_Port GPIOA
#define BAT_ADC_Pin GPIO_PIN_0
#define BAT_ADC_GPIO_Port GPIOB
#define BRAKE_LIGHT_Pin GPIO_PIN_8
#define BRAKE_LIGHT_GPIO_Port GPIOA
#define SERVO_OUT_Pin GPIO_PIN_9
#define SERVO_OUT_GPIO_Port GPIOA

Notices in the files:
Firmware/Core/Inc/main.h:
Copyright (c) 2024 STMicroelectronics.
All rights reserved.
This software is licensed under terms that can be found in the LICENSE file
